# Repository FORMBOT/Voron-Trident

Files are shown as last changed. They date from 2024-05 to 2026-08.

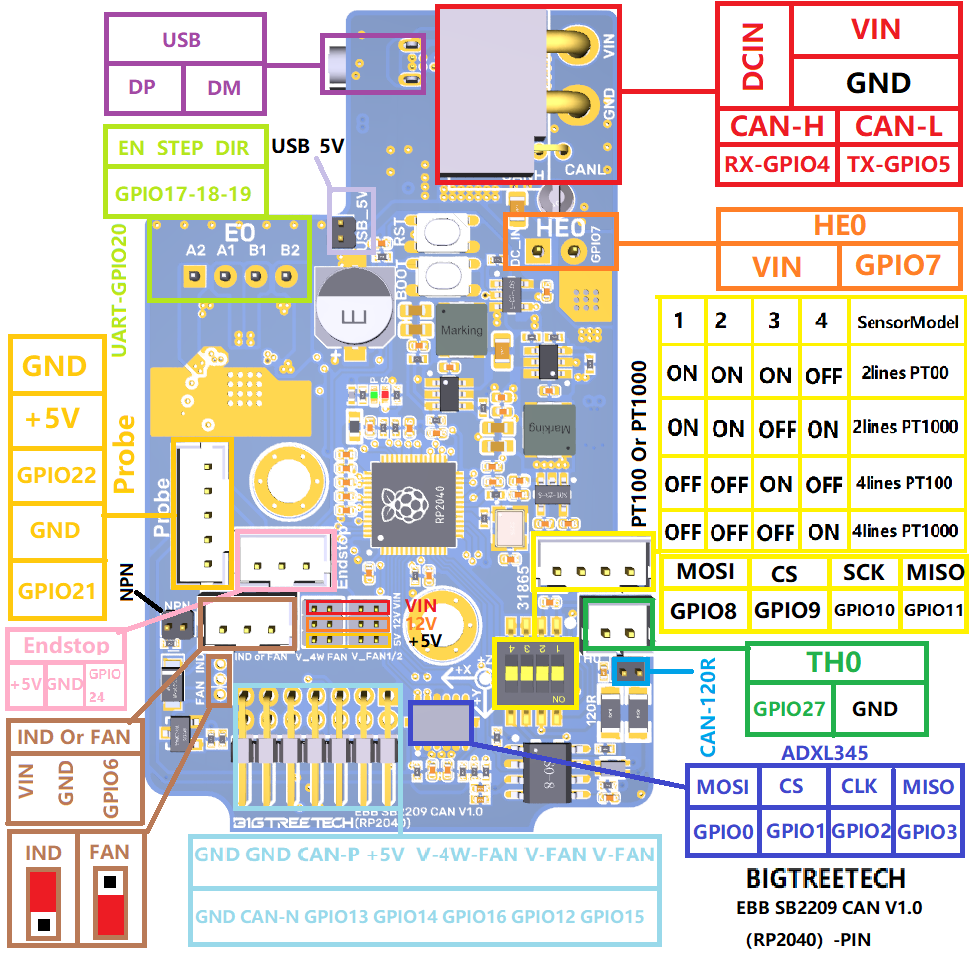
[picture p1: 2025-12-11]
Diagrams/Pins/SB2209 RP2040 Pinout.png

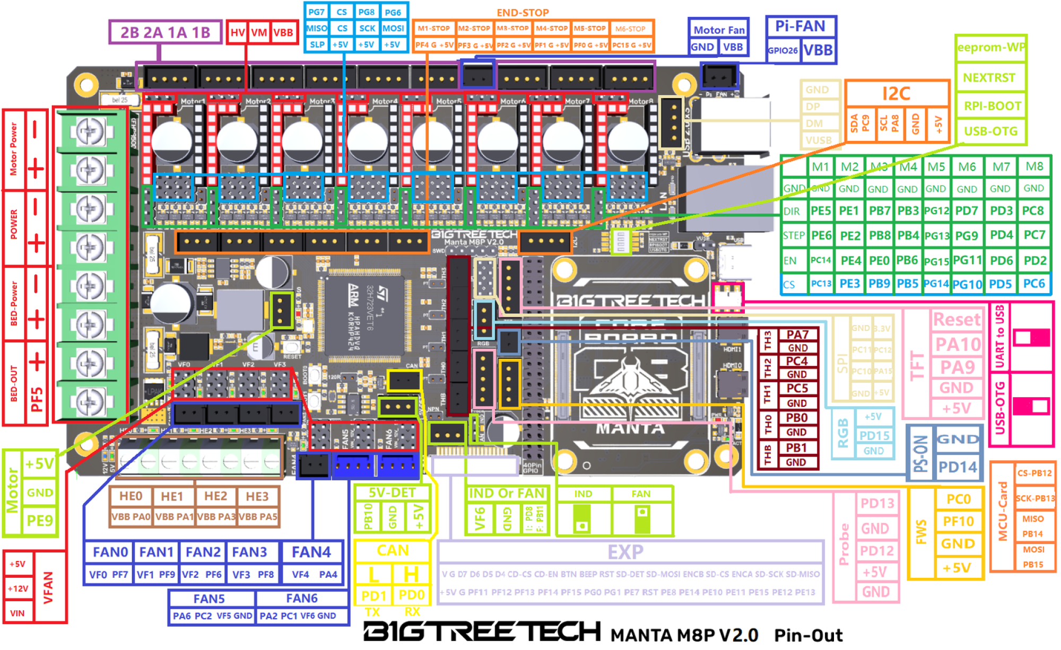
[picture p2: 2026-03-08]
Diagrams/Pins/BIGTREETECH MANTA M8P V2-0 PinOut.png

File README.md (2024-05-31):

# Custom STL´s for the Formbot Voron-Trident R1 Pro Kit
https://www.formbot3d.com/products/voron-trident-r1-pro-corexy-3d-printer-kit-with-best-quality-parts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

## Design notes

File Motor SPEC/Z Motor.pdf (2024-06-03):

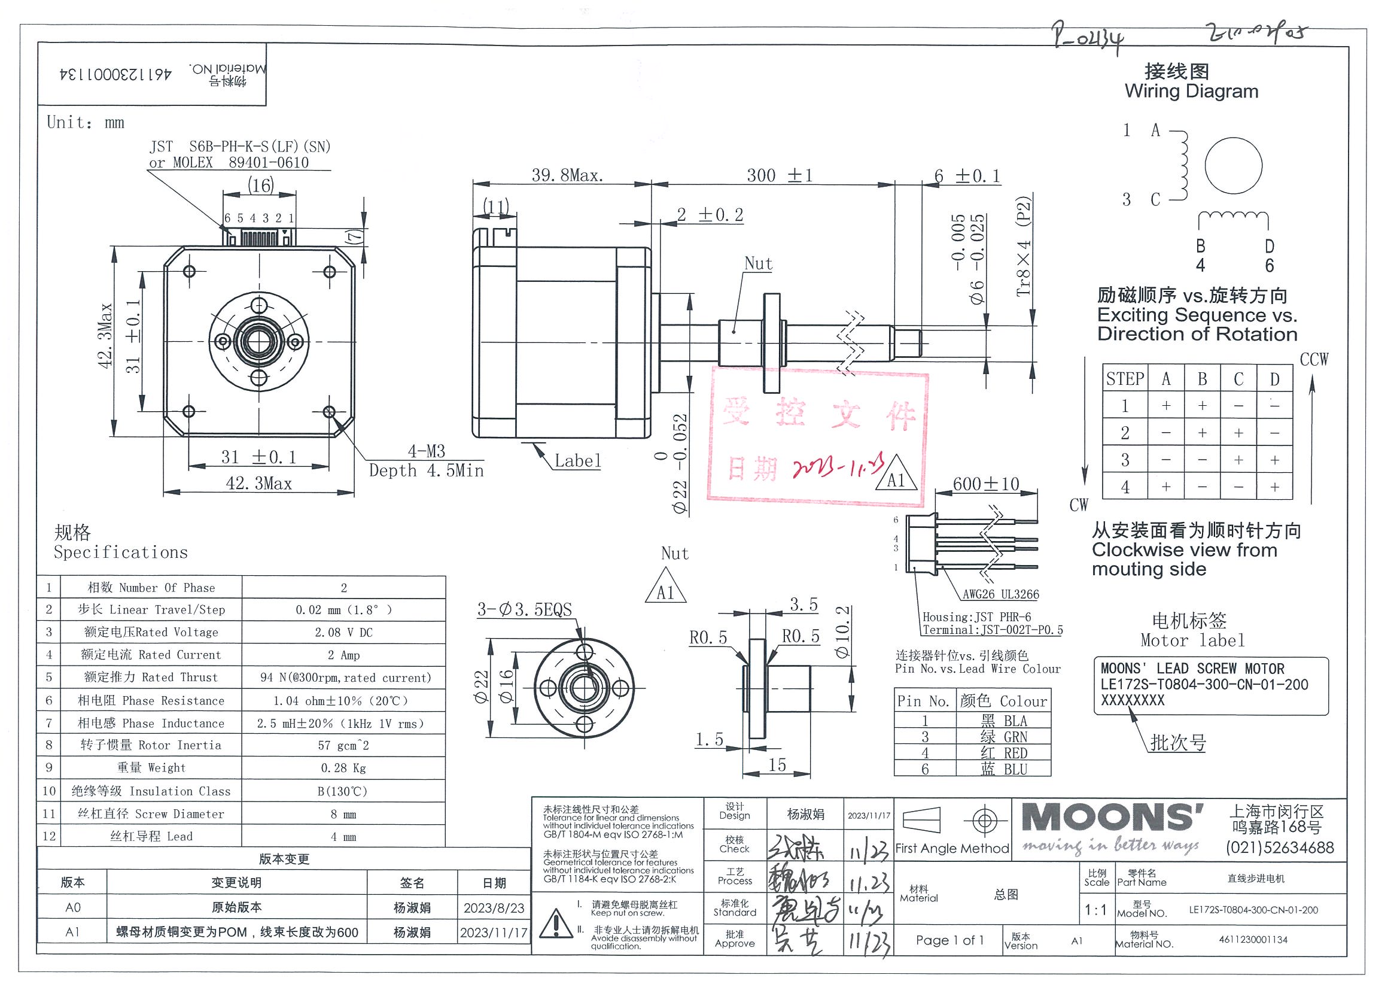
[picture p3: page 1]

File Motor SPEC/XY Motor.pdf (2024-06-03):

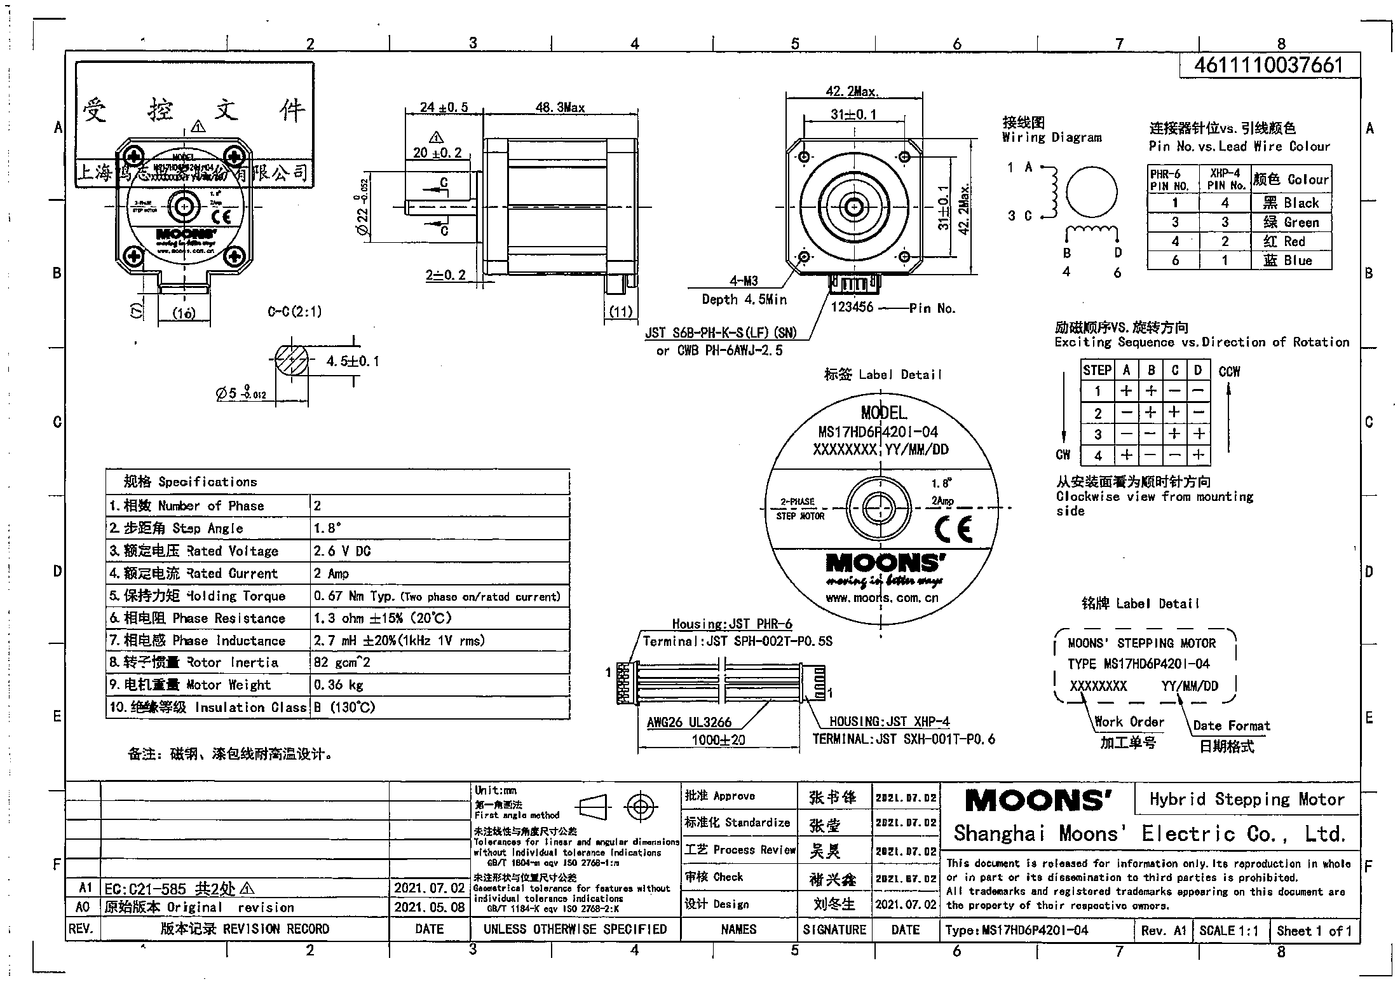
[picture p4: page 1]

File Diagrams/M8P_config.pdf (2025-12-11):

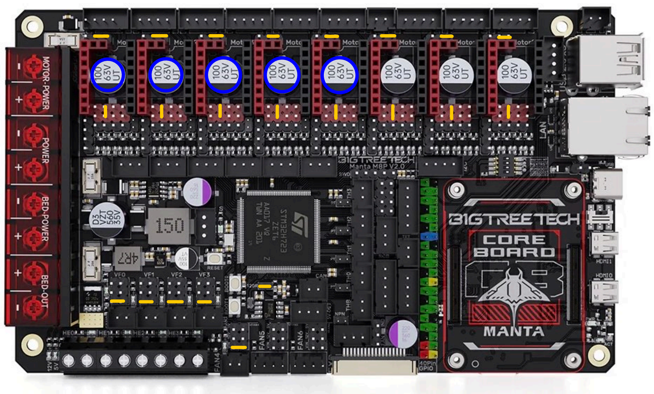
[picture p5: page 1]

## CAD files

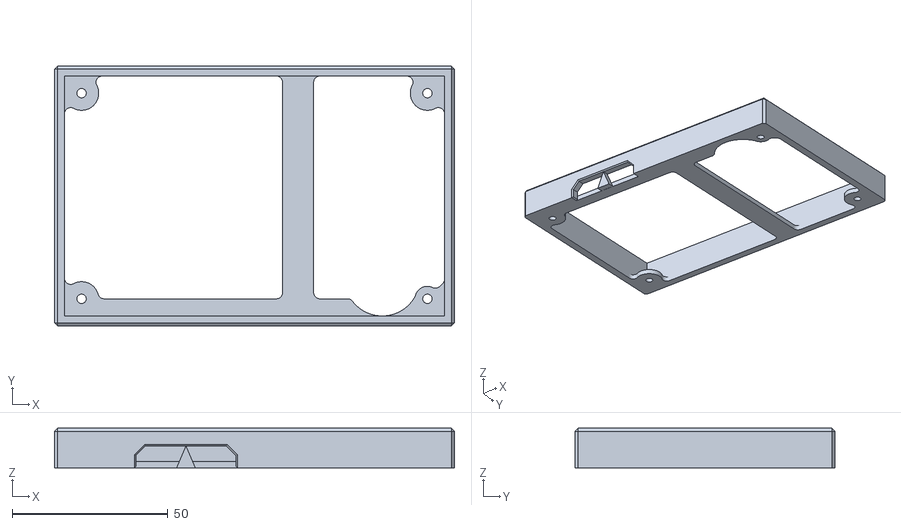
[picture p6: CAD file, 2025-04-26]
STL/Accent/BTT HDMI5 V1_2 mount frame_Regular.stl
128.4 x 83.4 x 12.7

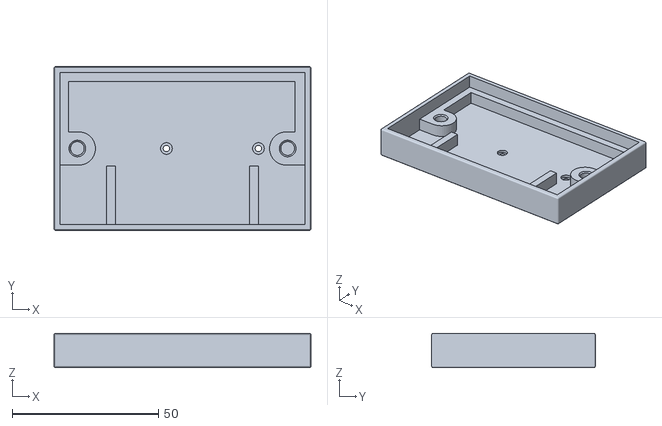
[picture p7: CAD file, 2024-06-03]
STL/Primary/3-6.STL
88.0 x 56.0 x 11.8

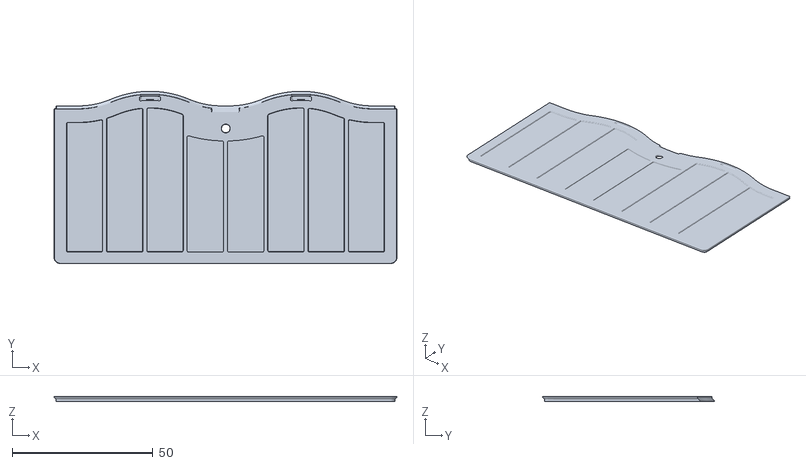
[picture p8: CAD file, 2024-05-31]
STL/Primary/Nevermore/Trident_Bed_Mount_XL_Cartridge_LID.stl
122.0 x 61.3 x 1.78

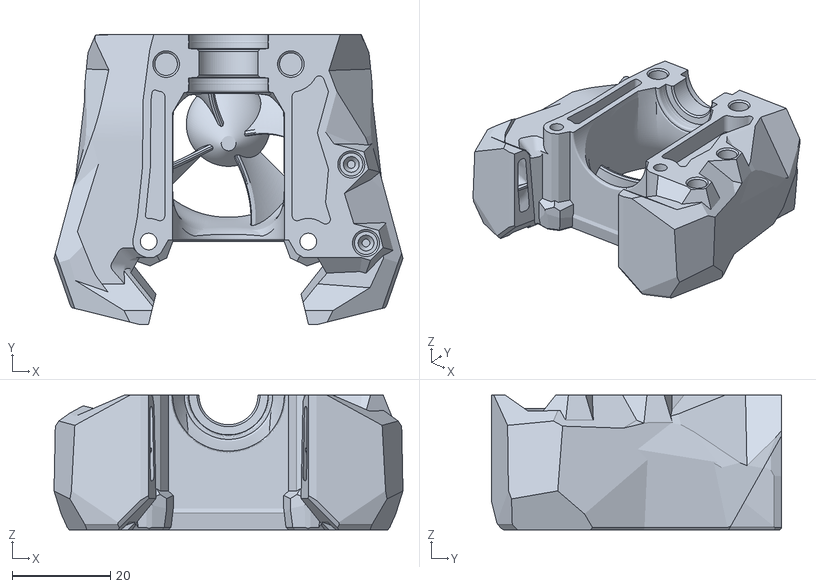
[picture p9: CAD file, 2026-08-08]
STL/Stealthburner/Stealthburner/stealthburner_printhead_v6_r6_front.stl
71.1 x 59.1 x 27.4

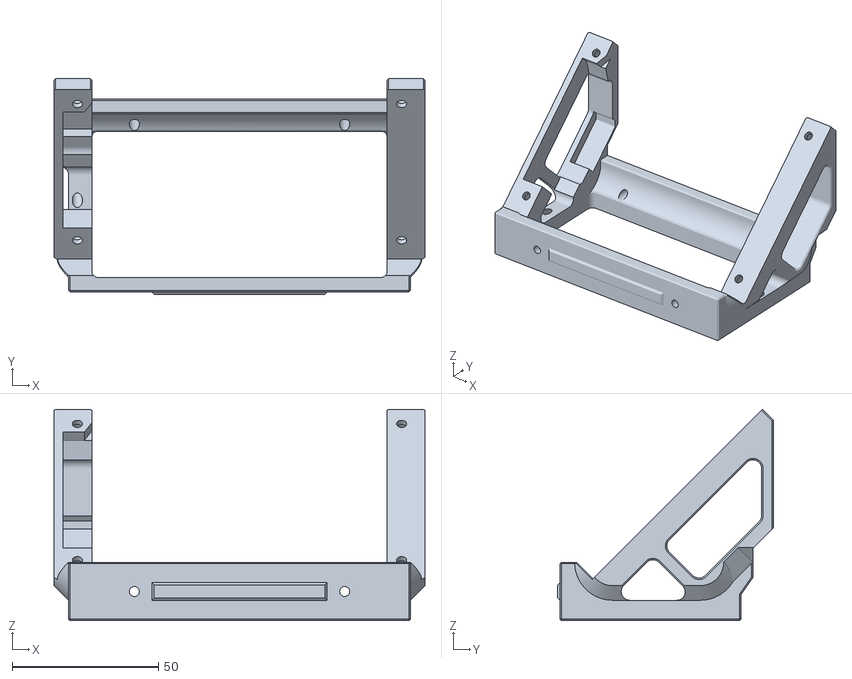
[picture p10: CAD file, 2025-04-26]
STL/Accent/BTT HDMI5 V1_2 mount bracket_Regular.stl
127.0 x 73.8 x 72.4

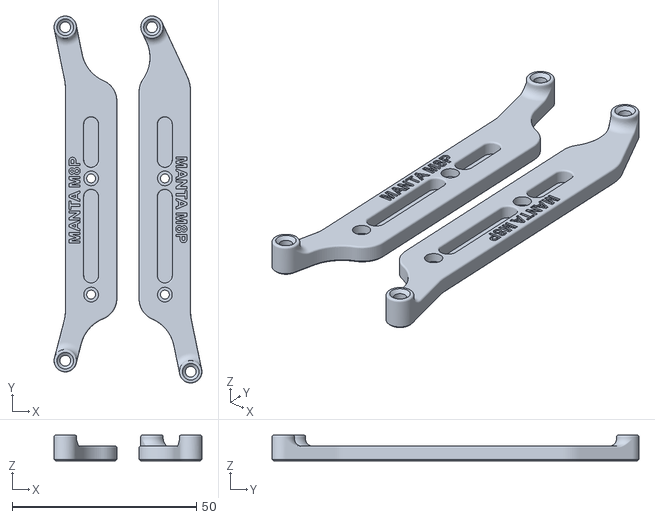
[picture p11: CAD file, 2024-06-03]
STL/Primary/Manta_M8P_2pc.stl
40.1 x 99.5 x 7.00

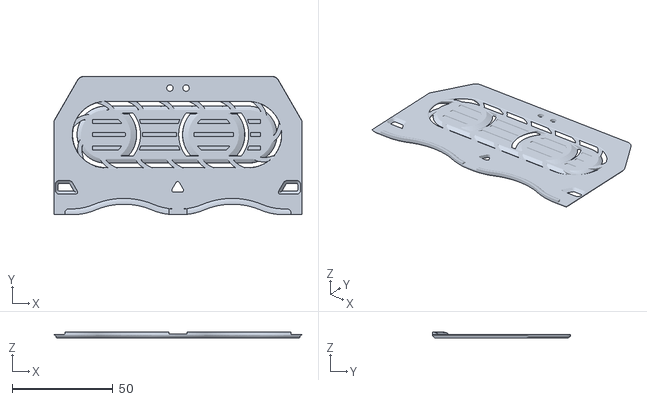
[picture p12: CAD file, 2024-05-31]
STL/Primary/Nevermore/Trident_Bed_Mount_Plenum_Lid_r1.stl
122.8 x 68.5 x 2.80

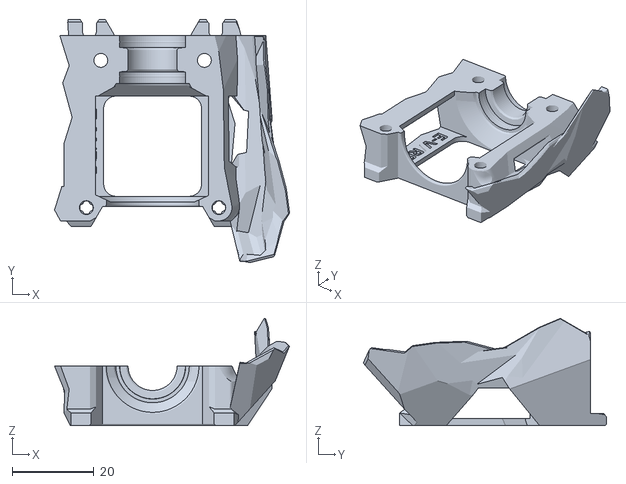
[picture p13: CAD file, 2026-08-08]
STL/Stealthburner/Stealthburner/stealthburner_printhead_v6_r6_rear_cw2.stl
57.7 x 59.7 x 26.3

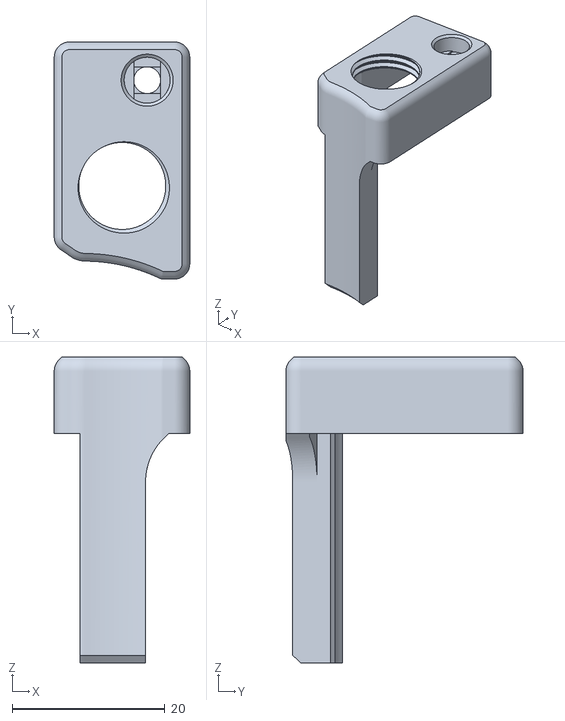
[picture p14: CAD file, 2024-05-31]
STL/Accent/PG7 Gantry Adapter.stl
17.7 x 31.0 x 40.0

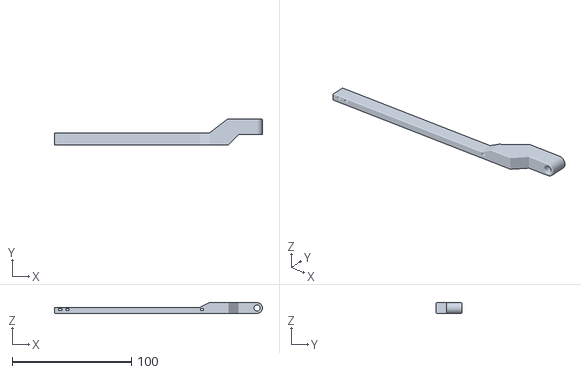
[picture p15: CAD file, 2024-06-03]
STL/Primary/cable support rod for CAN.STL
174.5 x 21.5 x 9.00

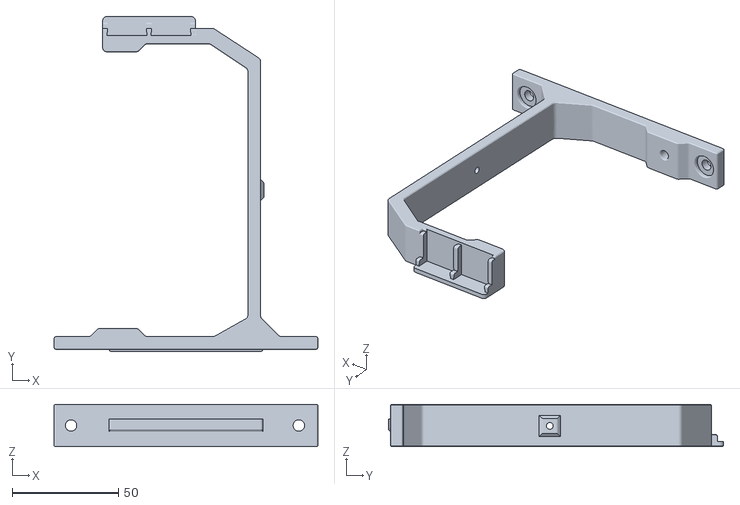
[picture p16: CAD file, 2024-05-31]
STL/Primary/Nevermore/trident_bed_mount_bracket_right_r1.stl
124.4 x 157.9 x 20.0

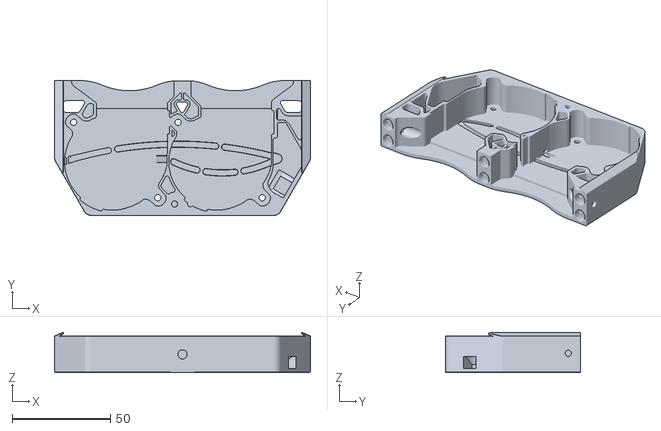
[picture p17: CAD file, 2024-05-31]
STL/Primary/Nevermore/Trident_Bed_Mount_Plenum.stl
130.0 x 68.6 x 20.5

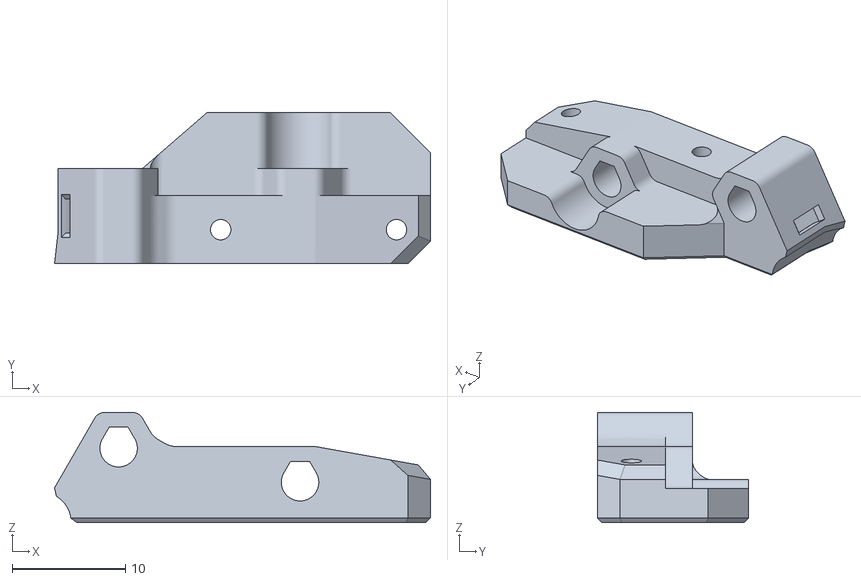
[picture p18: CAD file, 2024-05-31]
STL/Primary/sb_adxl_mount_generic_15.5mm_c_c.stl
33.2 x 13.4 x 9.70

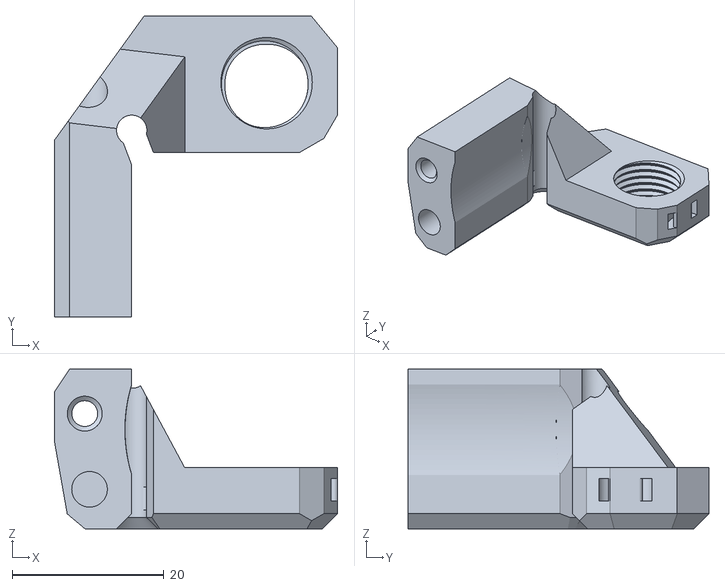
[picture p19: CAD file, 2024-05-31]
STL/Primary/Anchor v2.stl
37.3 x 39.7 x 21.1

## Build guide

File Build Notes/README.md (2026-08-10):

## Functional parts build notes (to get the Printer up and running)

Start with the [Stock Voron Trident R1 Manual](https://drive.google.com/file/d/1SZPV2CbrWAcEAtXU0fp9lZ_o1P9Tl-v9/view?usp=sharing) (the one on the Voron Trident R1 Git is not the most recent one).

Be aware that the vT Manual uses a 250mm Version of the Trident, so some dimensions may seem wrong if you build a 300mm/350mm Version.

### P. 48 Trident manual:

Skip this step, we use physical endstops and no hall effect ones.

### P. 56-60 Trident manual:

If you are building a 300mm machine you will need to start you screws from the second screw hole in the rails leaving the end holes open to allow space for T-nuts at later steps. Small reminder: The carriages are designed to slide along the rail easily. This unfortunately also includes sliding off the rails. Dropping the carriage likely irreparably damages it. ALWAYS put the little black rubber Carriage stoppers back on the rail (into the holes without screws) until your printer ist up and runnning!

### P. 100-101 Trident manual:

Skip these steps, you wont use either the inductive probe or a Cable chain on XY.

### P. 111 Trident manual:

Again, if you are building a bigger printer than the 250mm version, start at the outer holes and screw the rail down every second hole. Small reminder (again): The carriages are designed to slide along the rail easily. This unfortunately also includes sliding off the rails. Dropping the carriage likely irreparably damages it. ALWAYS put the little black rubber Carriage stoppers back on the rail (into the holes without screws) until your printer ist up and runnning!

### P.114 Trident manual:

Install all 4 screws on the right XY Joint.

### P. 115 Trident manual:

Leave this step out, you dont use a cable chain on X and Y.

### P. 122-123 Trident manual:

You use a different X carriage / Probe. Fix the belts with some tape and proceed with the belt Routing. After you routed the belts, fix them on the other side with some tape as well.

### P. 131-133 Trident manual:

Skip these steps, you will do it later after tap is assembled.

### P. 133 Trident manual:

X Carriage: After finishing the AB-Belts Routing, switch to the [TAP Manual](https://github.com/VoronDesign/Voron-Tap/tree/main/Manual). Optotap is used as the sensor.

Be sure to take a look into the R8\_errata.md document, it Highlights some important changes from the Manual and install the X Endstop switch.

### P. 33 Tap Manual:

After you have installed Tap successfully and have the AB belts fixed in the tap carriage, switch to page 134 of the Trident Manual.

### P. 135-137 Trident manual:

Skip these steps since you don't use the stock X carriage but instead you use tap.

### P. 144-145 \& 159 Trident manual:

You don't use this endstop. Your endstop is Tap.

### P. 162/163 Trident manual:

Switch to the [Stealthburner manual](https://github.com/VoronDesign/Voron-Stealthburner/tree/main/Manual).

### P. 13 Stealthburner manual:

You use a Toolhead PCB, so install these two heat inserts.

### P. 14 Stealthburner manual:

Skip

### P. 30 Stealthburner manual:

Follow [this Video Guide](https://www.youtube.com/watch?v=ly22qmB3NxE&t=1s) on how to set the gear mesh on your CW2.

Follow [this video Guide](https://www.youtube.com/watch?v=L1gxBCiE0pk) on how to set the Anti-Squish as well.

### P. 31 Stealthburner manual:

Skip for now, we will install our Version of the Anchor later.

### P. 34 Stealthburner manual:

You dont need to fix the Cable Cover down with the m3x6 BHCS now, you will need to access this later.

### P. 36-43 Stealthburner manual:

All Hotends are mounted in a similar pattern and pretty self-explaining, your hotend mount and hotend will look different.

### P. 46-51 Stealthburner manual:

Be very careful with the cables, you can easily rip them off the LED PCB which leads to this LED and the following ones not working.

### P. 53 Stealthburner manual:

Be sure that your fan blows in the right Direction. Look at the arrows on the fan. Additionally, the Sticker on the fan is on the back pointing towards the Hotend. You want the fan to blow air into the hotend, not trying to pull the air out. This destroys your fan and your whole hotend mount because of heatcreep.

### P. 56 Stealthburner manual:

You dont need to screw the 5015 fan into the SB Face, you will install the SB0000 Fan PCB there later.

### P. 58 Stealthburner manual:

All parts of the Stealthburner are now pretty much finished. Now you will need to install the Can-Board on there and do some basic wiring. Switch to the [SB2209 RP2040 Manual](https://github.com/bigtreetech/EBB/tree/master/EBB%20SB2209%20CAN%20%28RP2040%29/Build%20Guide).

### P. 02 SB2209 manual:

Now you need to screw down the 5015 fan with the SB0000 PCB :)

### P. 03/04 SB2209 manual:

You need to select Vin (24V) for all fans. Be sure to wire Gnd to Gnd and 24V to 24V! Otherwise you will experience magic smoke later.

### P. 05 SB2209 manual:

Skip

### P. 06 SB2209 manual:

Be sure to wire Gnd to Gnd, Signal to Signal and 24V to 24V! Otherwise you will experience magic smoke later.

### P. 13 SB2209 manual:

You Need to set the switch to 1: on; 2: on; 3: off; 4: on

### P. 15 SB2209 manual:

Skip

### P. 16 SB2209 manual:

Be sure to use the endstop labeled "To CAN\_Endstop" which is the one with the short wires.

### P. 18 SB2209 manual:

Skip

### P. 19 SB2209 manual:

Skip, Stealthburner will be assembled later.

### P. 24 SB2209 manual:

You will need to Strip down the Isolation a bit so you have enough cable length to connect the cable to the PSU and to the Can port. Go back to the Tap Manual page 34 now, flashing the toolhead will be done later.

Use the tight cable sleeve around the cable.

### P. 36 Tap manual:

Stealthburner and Tap are now completed and installed. Switch back to p. 164 of the original Trident manual.

### P. 173 Trident manual:

Rotate the din rails 90° compared to the original layout.

### P. 181-183 Trident manual:

Skip; Raspberry Pi mounting and 5v PSU mounting is not needed. Instead, mount the CB1 / CM4 on the Manta.

### P. 191 Trident manual:

You use the 3in6 Power Distributor instead.

### P. 195 Trident manual:

another small reminder, you don't use a 5v PSU.

### P. 196 Trident manual:

small reminder, you dont use a Raspberry Pi.

### P.198-200 Trident manual:

Skip; TAP is your Z-Endstop, your X Endstop sits on Tap and your Y endstop will be mounted on the A Motor mount later.

### P. 202-205 Trident manual:

Skip these steps, instead configure your Manta like this:

[M8P\_v2 Jumper / Driver marking](https://github.com/FORMBOT/Voron-Trident/blob/main/Diagrams/M8P_config.pdf)

Place a Jumper on all yellow marked pins and place the TMC2209s with attached heatsink on all driver ports with a blue circle after installing the jumpers.

### P. 210/211/216 Trident manual:

Leave the cables to the 5v PSU out.

### P. 217 Trident manual:

Skip, you dont use a standart Raspberry.

### P. 218 Trident manual:

The Z-Endstop cables are not needed.

### P. 218-219/221-231/233-237 Trident manual:

For a better Overview of the wiring, use the [wiring diagram](https://github.com/FORMBOT/Voron-Trident/blob/main/Diagrams/Wiring%20Diagram%20of%20Trident%20R1%20Pro.pdf).

Connect the B motor (left motor) to X Motor, connect the A motor (right motor) to Y Motor.

Connect the CAN-Cable to the right CAN-Port on the M8P and 24V / GND to the 24V PSU. If you think the cables are not Long enough, you haven't done [this step](https://github.com/FORMBOT/Voron-Trident/tree/main/Build%20Notes#p-24-sb2209-manual).

### P. 232 Trident manual:

Route the Y Endstop cable and the A Motor cables down like the B Motor cable (but on the right side of the printer).

### P. 242-244/257 Trident manual:

Skip these steps and instead mount the klipperscreen.

### P. 258 Trident manual:

Don't close the electronics compartment yet, you will need to acces this while flashing the boards.

### P. 281 Trident manual:

Use the big cable sleeve around the exhaust fan cable (if you use the stock exhaust).

#### Don't power on the printer if you are not 100% sure you wired everything correct! And have a look into [this](https://github.com/FORMBOT/Voron-Trident/blob/main/Diagrams/Instruction%20of%20Trident%20R1%20Pro.pdf).

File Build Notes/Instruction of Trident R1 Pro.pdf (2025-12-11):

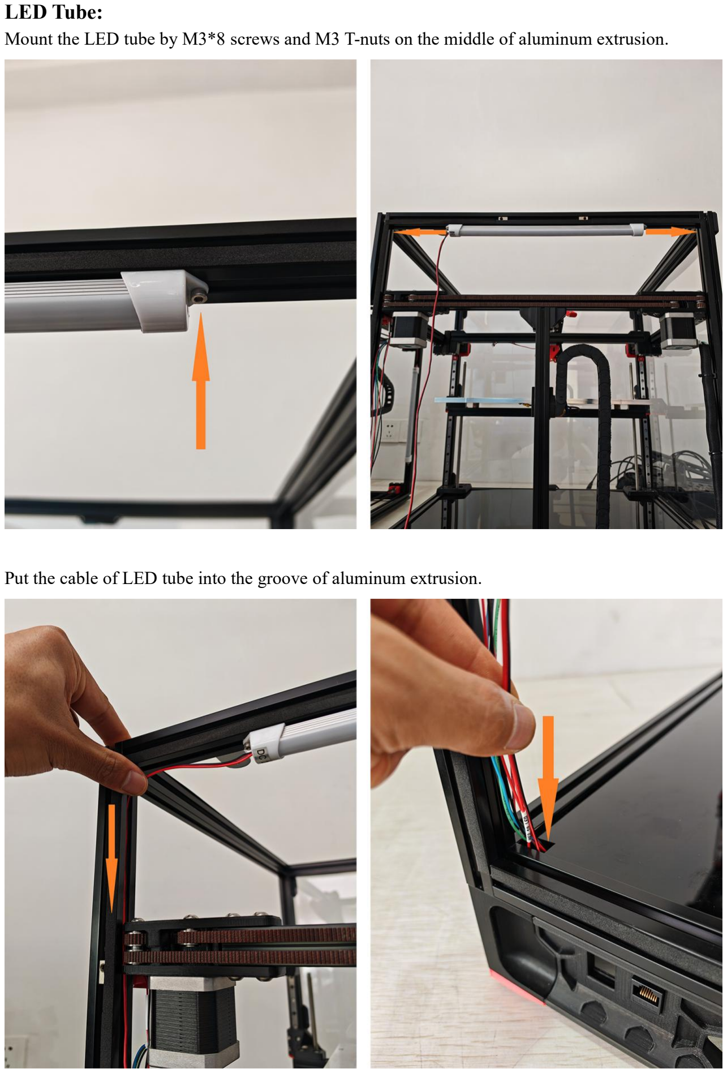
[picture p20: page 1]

LED Tube:
Mount the LED tube by M3*8 screws and M3 T-nuts on the middle of aluminum extrusion.

Put the cable of LED tube into the groove of aluminum extrusion.

Plug the cable onto mainboard as showed below, the red wire to “+”, the black wire to “-”.

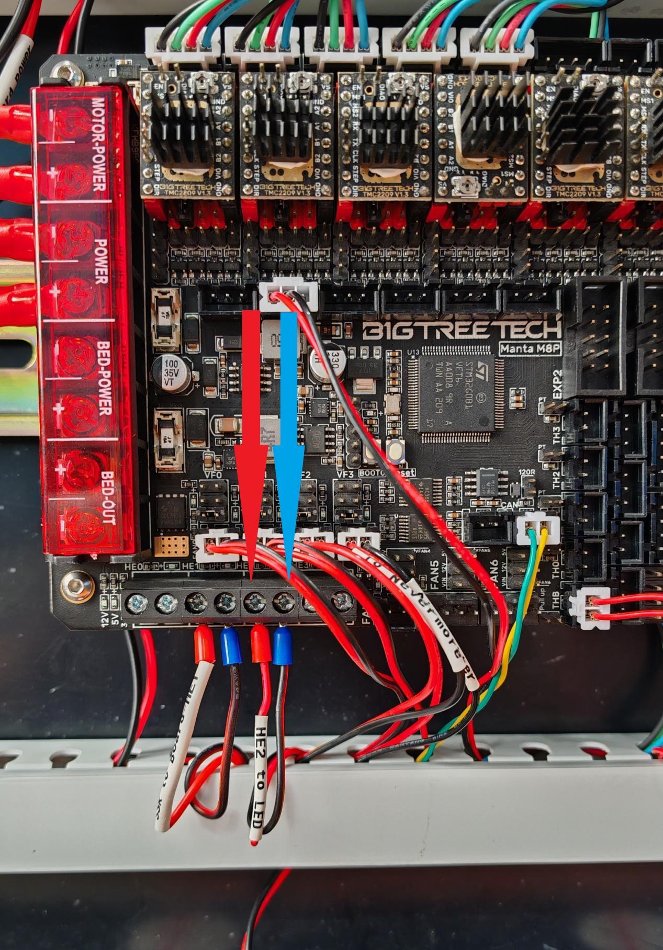
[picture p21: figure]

Filament Runout Sensor:
Take out the sensor and cable as showed below.

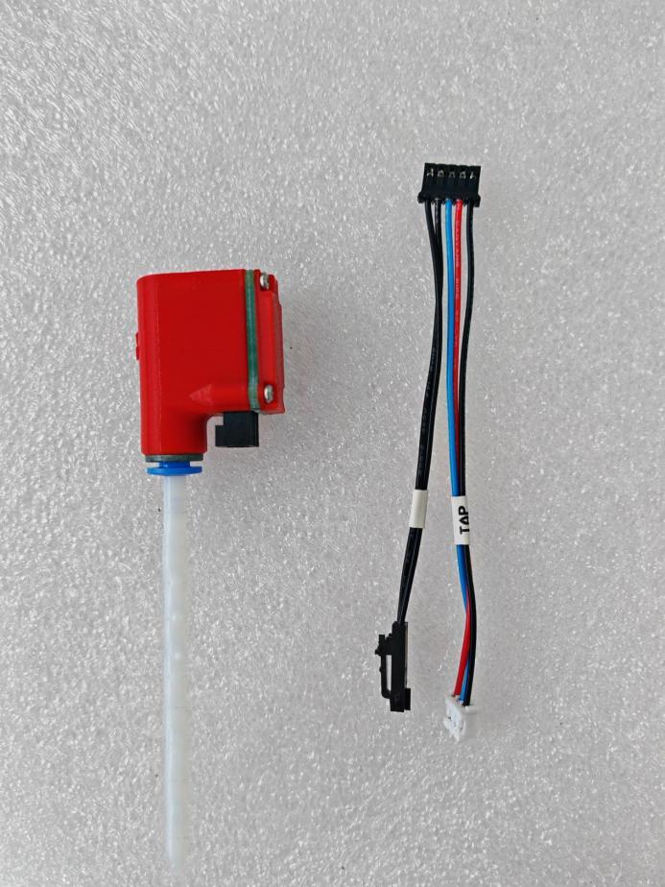
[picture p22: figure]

Plug the cable into below connector on extruder.

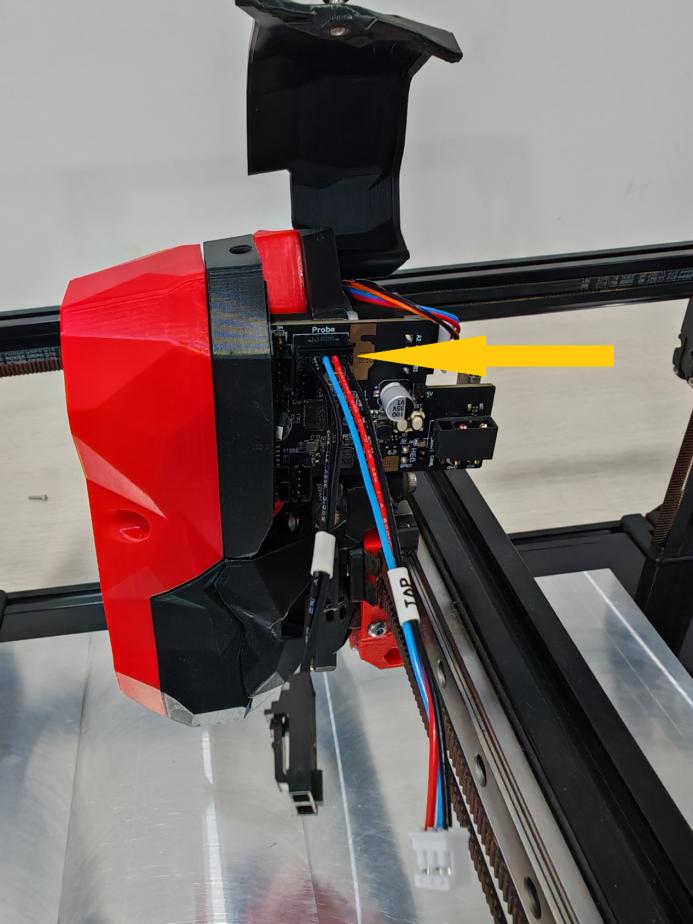
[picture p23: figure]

Plug the wires of TAP to below connector.

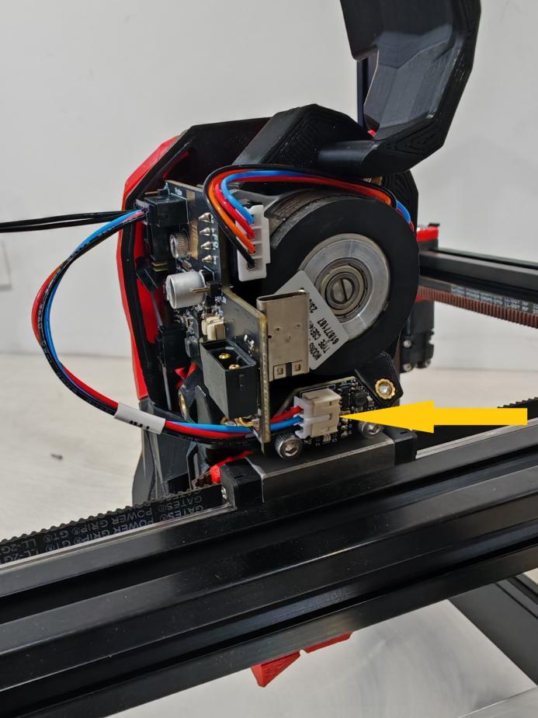
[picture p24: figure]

Pass the wires of filament runout sensor through below hole, then plug it onto sensor directly.

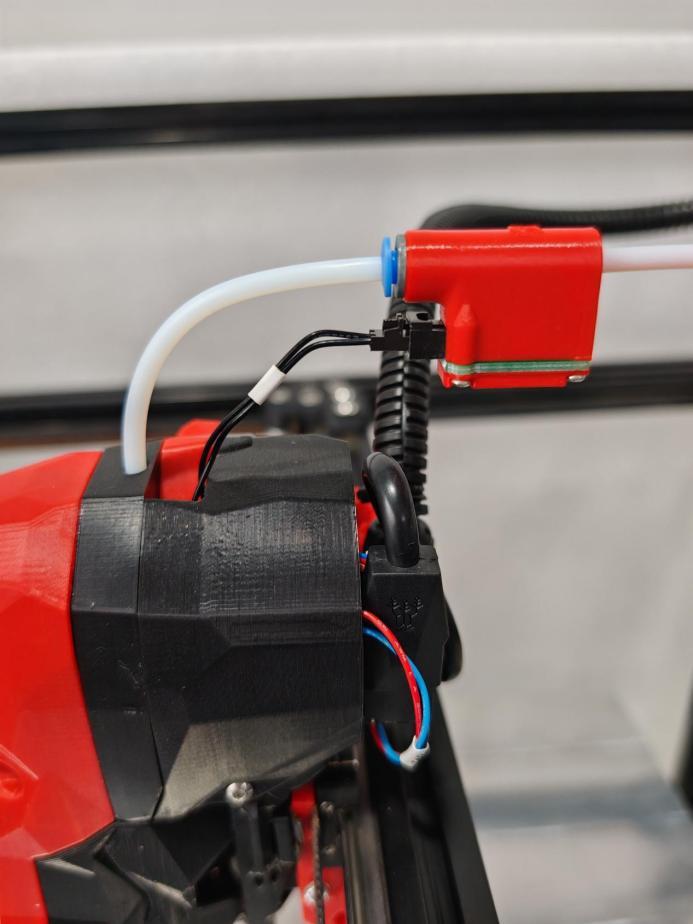
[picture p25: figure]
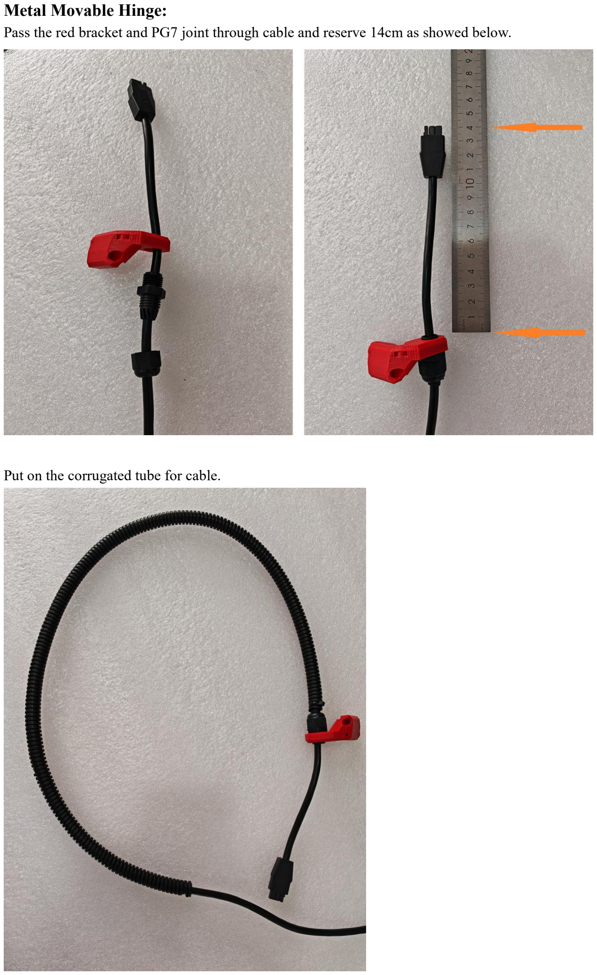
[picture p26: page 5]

Metal Movable Hinge:
Pass the red bracket and PG7 joint through cable and reserve 14cm as showed below.

Put on the corrugated tube for cable.

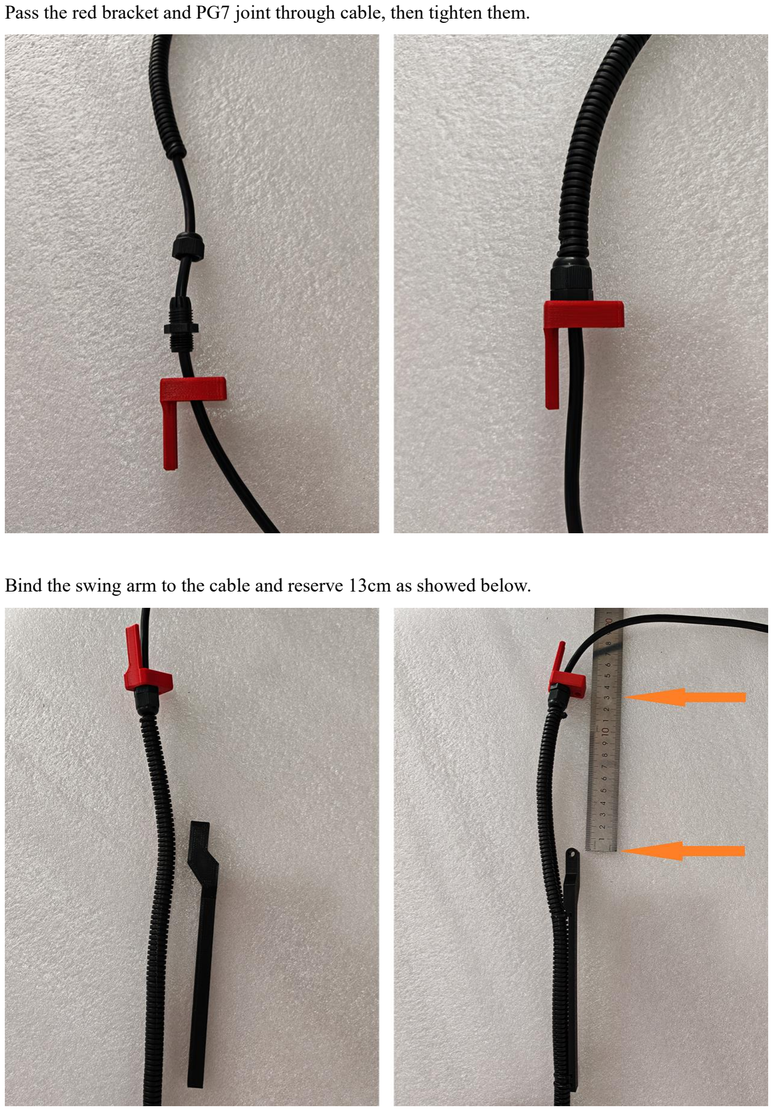
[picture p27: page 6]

Pass the red bracket and PG7 joint through cable, then tighten them.

Bind the swing arm to the cable and reserve 13cm as showed below.

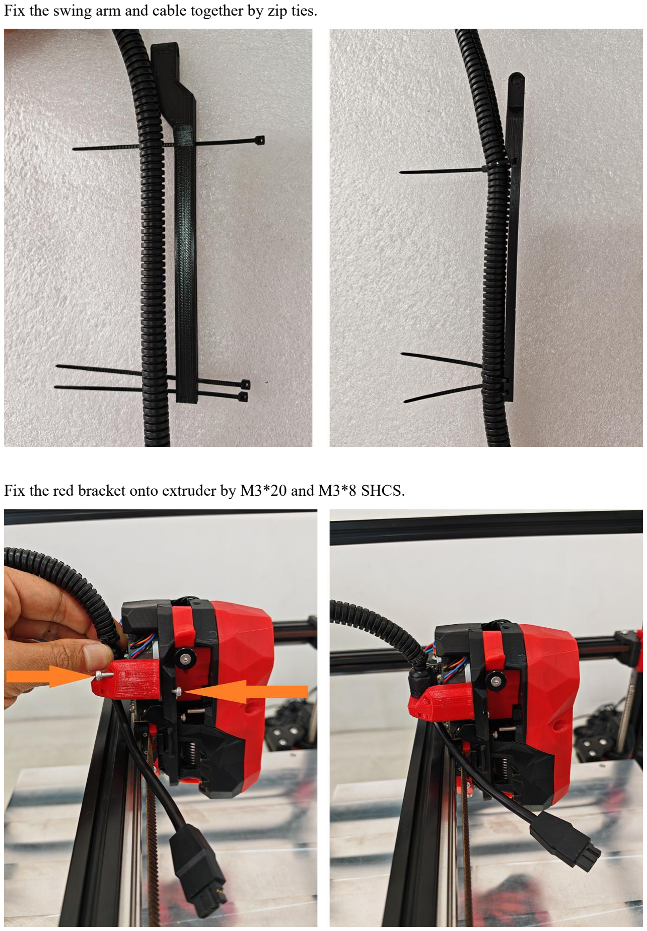
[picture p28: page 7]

Fix the swing arm and cable together by zip ties.

Fix the red bracket onto extruder by M3*20 and M3*8 SHCS.

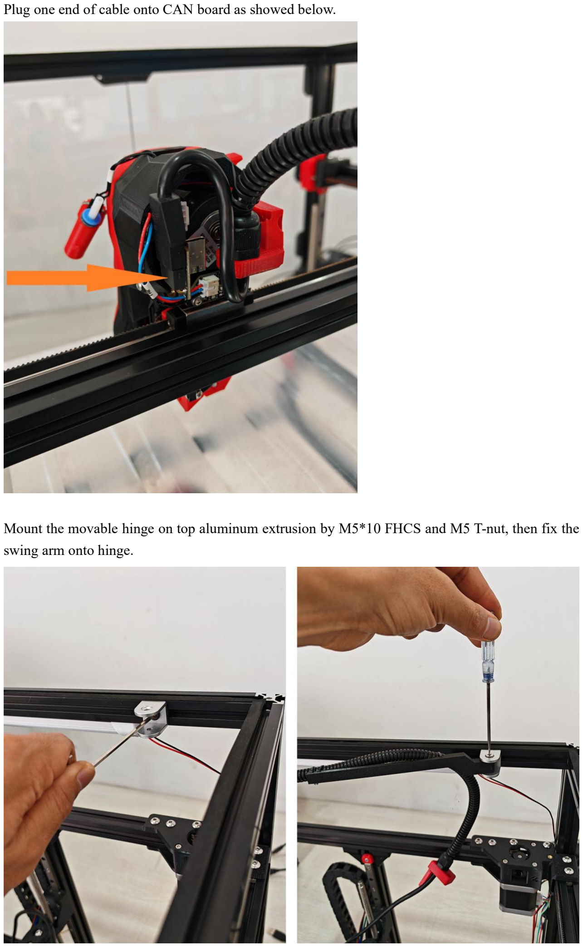
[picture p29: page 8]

Plug one end of cable onto CAN board as showed below.

Mount the movable hinge on top aluminum extrusion by M5*10 FHCS and M5 T-nut, then fix the swing arm onto hinge.

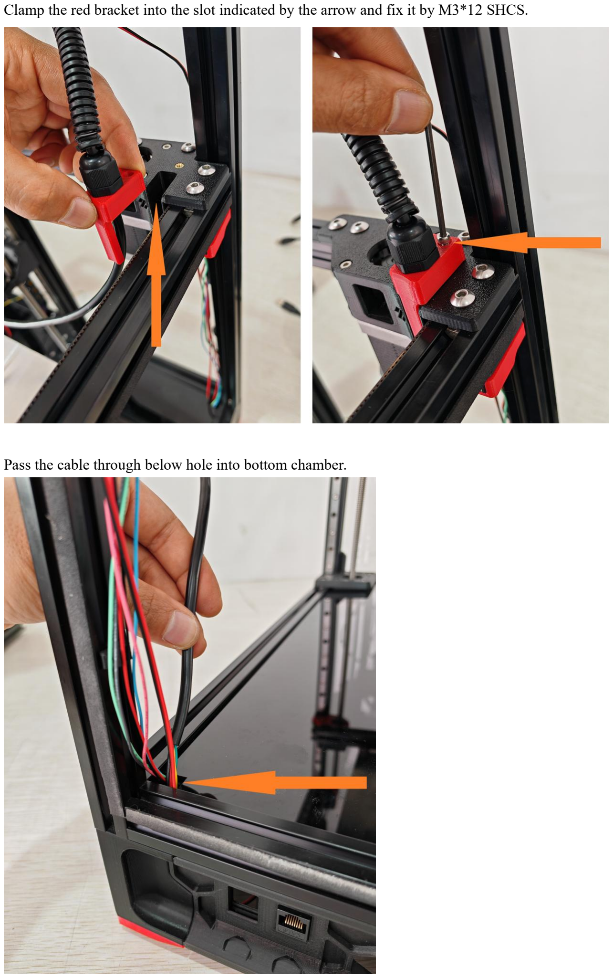
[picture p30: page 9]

Clamp the red bracket into the slot indicated by the arrow and fix it by M3*12 SHCS.

Pass the cable through below hole into bottom chamber.

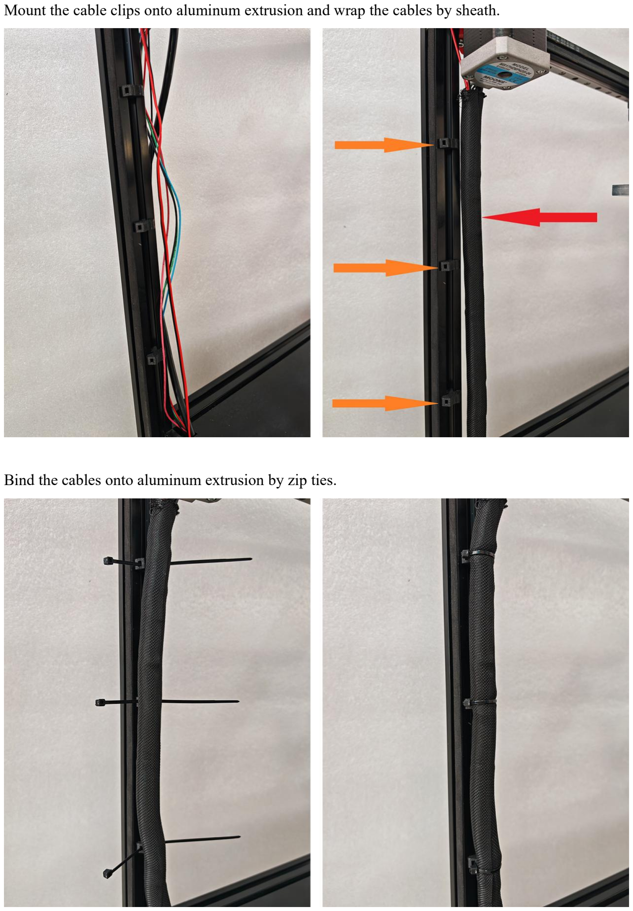
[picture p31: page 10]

Mount the cable clips onto aluminum extrusion and wrap the cables by sheath.

Bind the cables onto aluminum extrusion by zip ties.

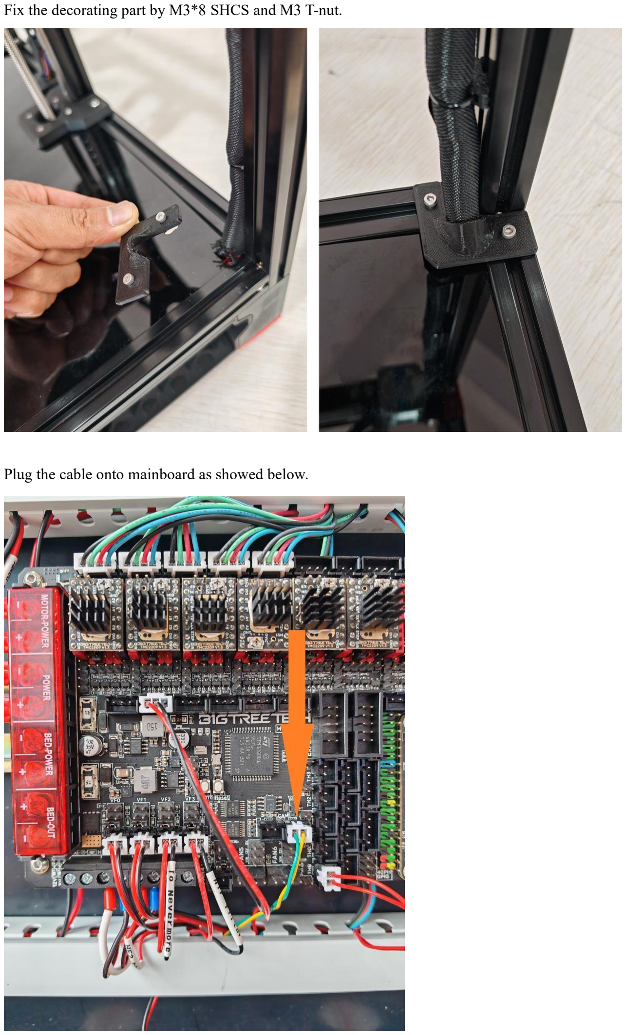
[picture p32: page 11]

Fix the decorating part by M3*8 SHCS and M3 T-nut.

Plug the cable onto mainboard as showed below.

Connect below two wires to power supply, the red wire to “+”, the black wire to “-”.

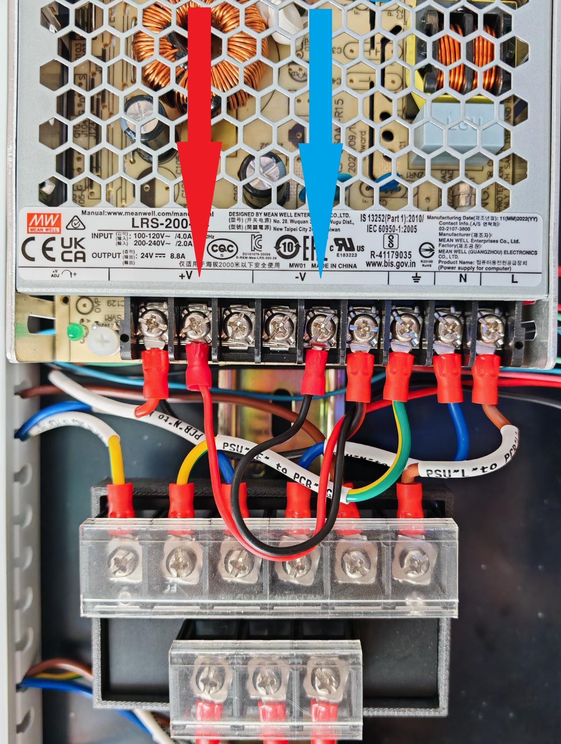
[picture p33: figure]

Nevermore Air Filter:
Iron M3 brass nuts into below holes.

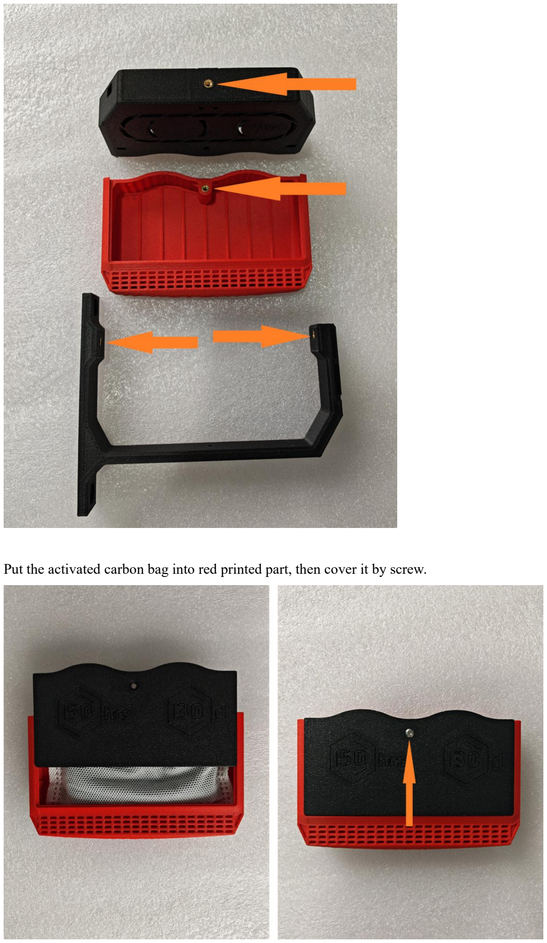
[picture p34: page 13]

Put the activated carbon bag into red printed part, then cover it by screw.

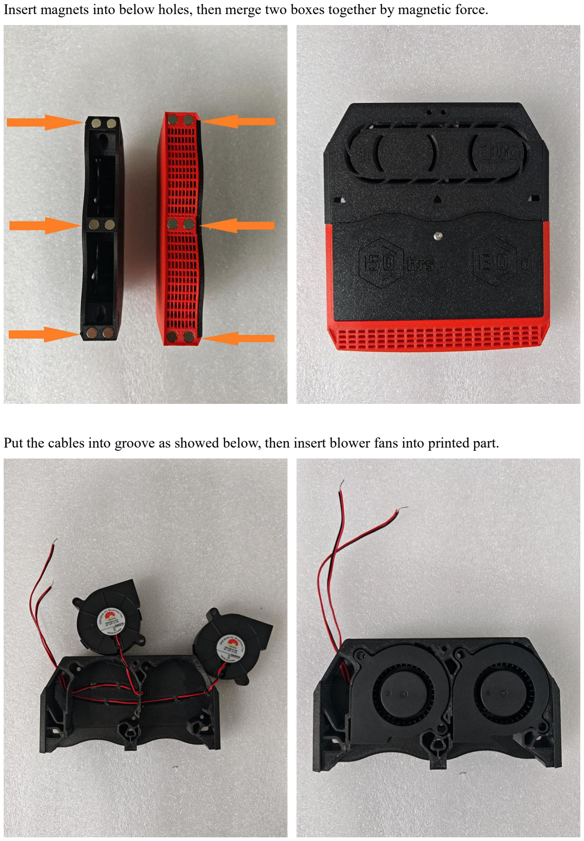
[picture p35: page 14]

Insert magnets into below holes, then merge two boxes together by magnetic force.

Put the cables into groove as showed below, then insert blower fans into printed part.

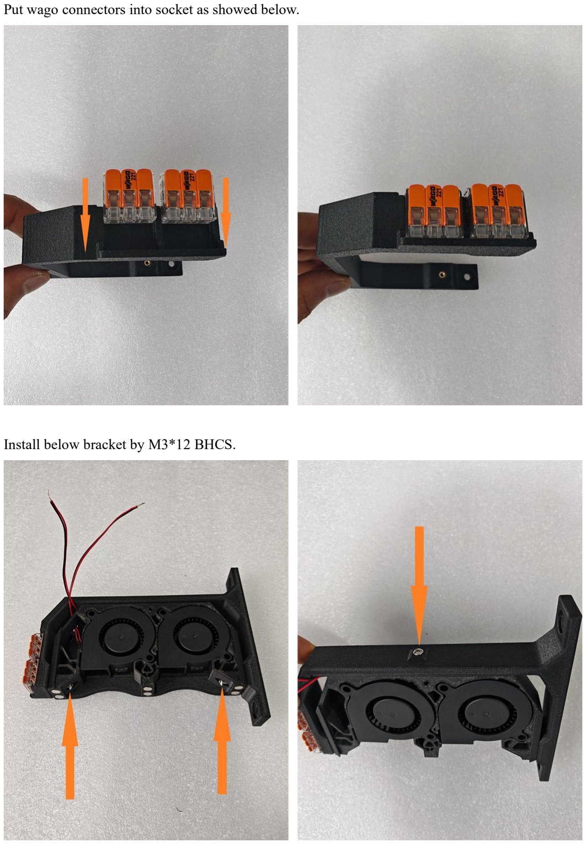
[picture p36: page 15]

Put wago connectors into socket as showed below.

Install below bracket by M3*12 BHCS.

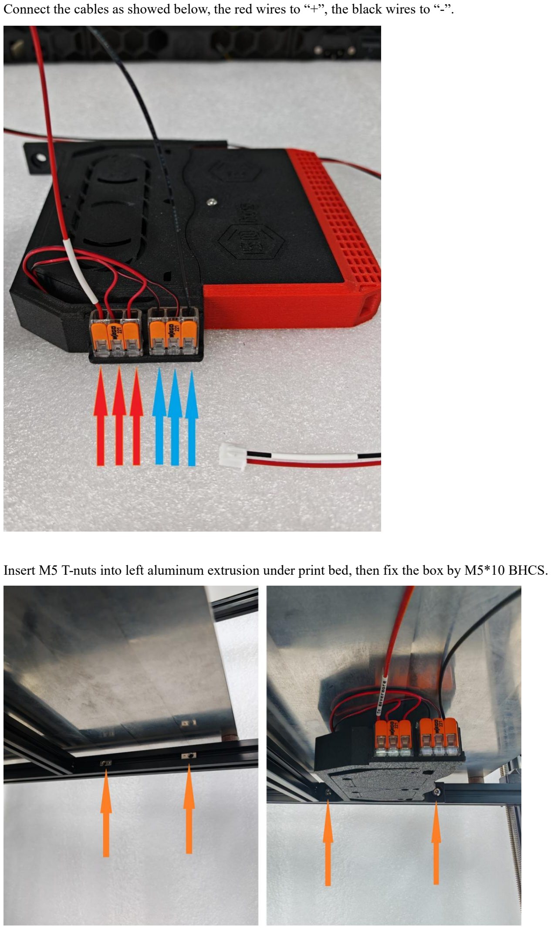
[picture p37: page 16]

Connect the cables as showed below, the red wires to “+”, the black wires to “-”.

Insert M5 T-nuts into left aluminum extrusion under print bed, then fix the box by M5*10 BHCS.

Merge two boxes together by magnetic force.

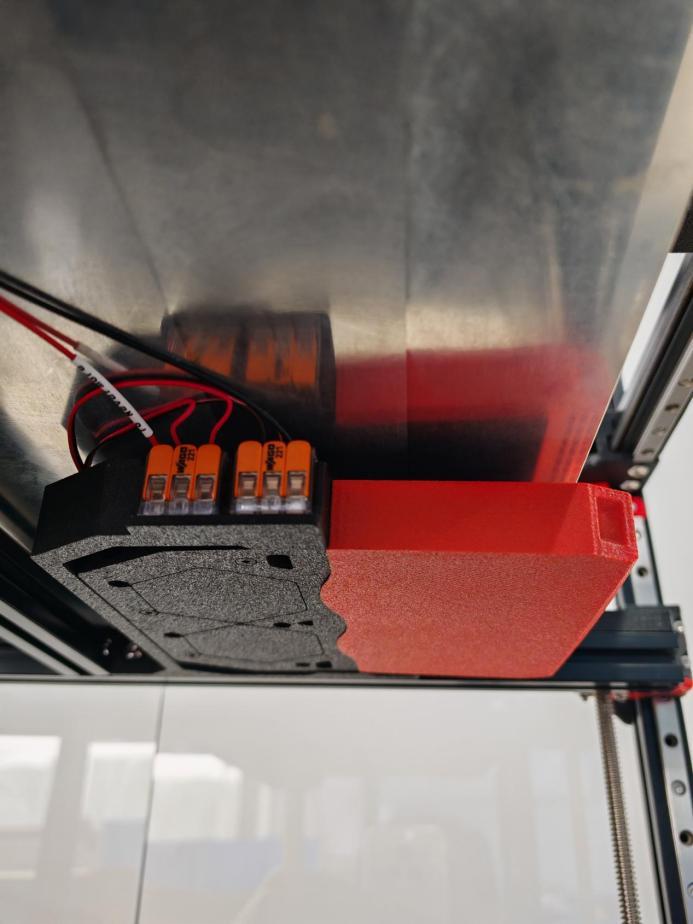
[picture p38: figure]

Pass the cables through chain into bottom chamber.

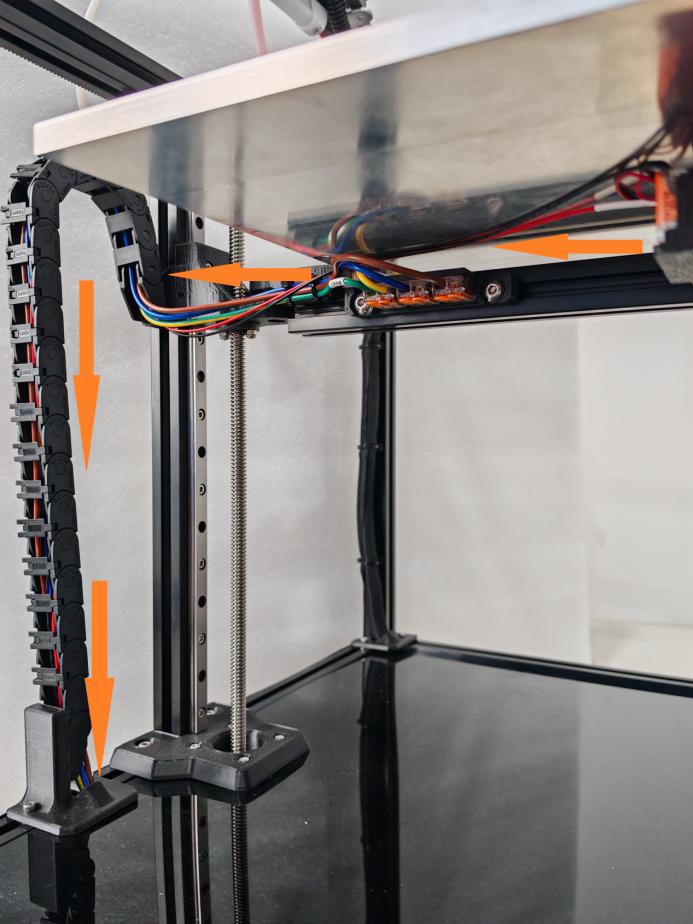
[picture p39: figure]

Finally, plug it onto mother board as showed below.

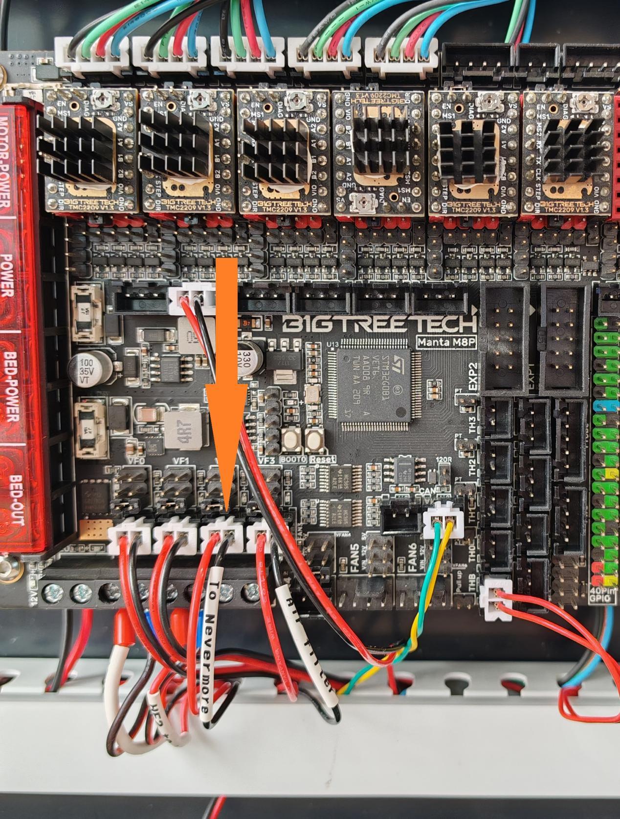
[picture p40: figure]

Referential Links:

Voron Official Build Guide: https://github.com/VoronDesign/Voron-Trident/tree/main/Manual

Stealthburner Extruder:
https://github.com/VoronDesign/Voron-Stealthburner/blob/main/Manual/Assembly_Manual_SB.p df (https://github.com/VoronDesign/Voron-Stealthburner/blob/main/Manual/Assembly_Manual_SB.pdf)

TAP R8 Leveling Sensor:
https://github.com/VoronDesign/Voron-Tap/blob/main/Manual/Assembly_Manual_Tap.pdf

HDMI 5" V1.2 Screen:
https://www.printables.com/model/926845-btt-hdmi5-v12-display-mount-voron

Manta M8P V2.0+CB1 Board:
https://github.com/bigtreetech/Manta-M8P/blob/master/V2.0/BIGTREETECH%20MANTA%20 M8P%20V2.0%20User%20Manual.pdf (https://github.com/bigtreetech/Manta-M8P/blob/master/V2.0/BIGTREETECH%20MANTA%20M8P%20V2.0%20User%20Manual.pdf)

EBB SB2209 CAN(RP2040):
https://github.com/bigtreetech/EBB
https://canbus.esoterical.online/

Umbilical Mount for CAN:
https://www.printables.com/model/326623-voron-trident-wire-cover-w-pg7-cable-gland-adapterhttps://www.printables.com/pl/model/464735-pg7-cnlinko-lp-12-mount-for-sb22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

Nozzle Clean Mod:
https://www.printables.com/model/413177-voron-trident-fixed-nozzle-scubber

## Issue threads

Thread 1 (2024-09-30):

Screen holder STL does not have indentation for audio jack port

MartijnGevaert, 2024-09-30:
Greetings, I noticed the touchscreen holder does not have a cutout for the audio jack, it does have one for the HDMI port next to it.
Simply extending the HDMI cutout to the side fixes the issue.

MartijnGevaert, 2024-09-30:
Did not see the accent part also needed.

Closed 2024-09-30.

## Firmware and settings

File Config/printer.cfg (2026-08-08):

[include mainsail.cfg]

[mcu]
canbus_uuid: YOU_DIDNT_CHANGE_ME_YET						# Insert the CANbus-UUID of your Manta from the firmware flashing steps

[mcu EBBCan]
canbus_uuid: YOU_DIDNT_CHANGE_ME_YET						# Insert the CANbus-UUID of your SB2209 RP2040 from the firmware flashing steps

[printer]
kinematics: corexy
max_velocity: 300  
max_accel: 10000
max_z_velocity: 15
max_z_accel: 350
square_corner_velocity: 5.0

[temperature_sensor MCU]
sensor_type: temperature_mcu

[temperature_sensor SoC]
sensor_type: temperature_host

#####################################################################
# 	X/Y Stepper Settings
#####################################################################

## X Stepper on Motor1(B Motor)
[stepper_x]
step_pin: PE6
dir_pin: PE5
enable_pin: !PC14
microsteps: 16
rotation_distance: 40
full_steps_per_rotation:200  #set to 400 for 0.9 degree stepper
endstop_pin: ^EBBCan:gpio24
position_min: 0
##--------------------------------------------------------------------

##	Uncomment below for 250mm build
#position_endstop: 250
#position_max: 250

##	Uncomment for 300mm build
#position_endstop: 300
#position_max: 300

##	Uncomment for 350mm build
#position_endstop: 350
#position_max: 350

##--------------------------------------------------------------------
homing_speed: 25   #Max 100
homing_retract_dist: 5
homing_positive_dir: true

##	Make sure to update below for your relevant driver (2208 or 2209)
[tmc2209 stepper_x]
uart_pin: PC13
interpolate: True
run_current: 0.9
sense_resistor: 0.110
stealthchop_threshold: 0

## Y Stepper on Motor2 (A Motor)
[stepper_y]
step_pin: PE2
dir_pin: PE1
enable_pin: !PE4
microsteps: 16
rotation_distance: 40
full_steps_per_rotation:200  #set to 400 for 0.9 degree stepper
endstop_pin: ^PF3
position_min: 0
##--------------------------------------------------------------------

##	Uncomment for 250mm build
#position_endstop: 250
#position_max: 250

##	Uncomment for 300mm build
#position_endstop: 300
#position_max: 300

##	Uncomment for 350mm build
#position_endstop: 350
#position_max: 350

##--------------------------------------------------------------------
homing_speed: 25  #Max 100
homing_retract_dist: 5
homing_positive_dir: true

##	Make sure to update below for your relevant driver (2208 or 2209)
[tmc2209 stepper_y]
uart_pin: PE3
interpolate: True
run_current: 0.9
sense_resistor: 0.110
stealthchop_threshold: 0

#####################################################################
# 	Z Stepper Settings
#####################################################################

## Z0 Stepper - Front Left on MOTOR3_A
[stepper_z]
step_pin: PB8
dir_pin: PB7
enable_pin: !PE0
# Rotation Distance for TR8x8 = 8, TR8x4 = 4, TR8x2 = 2
# rotation_distance: 4    
microsteps: 32
endstop_pin: probe:z_virtual_endstop
position_max: 250
position_min: -2.5
homing_speed: 8.0 # Leadscrews are slower than 2.4, 10 is a recommended max.
second_homing_speed: 3
homing_retract_dist: 3

##	Make sure to update below for your relevant driver (2208 or 2209)
[tmc2209 stepper_z]
uart_pin: PB9
interpolate: true
run_current: 0.6
sense_resistor: 0.110
stealthchop_threshold: 0

##	Z1 Stepper - Rear  on Motor5
[stepper_z1]
step_pin: PB4
dir_pin: PB3
enable_pin: !PB6
# Rotation Distance for TR8x8 = 8, TR8x4 = 4, TR8x2 = 2
# rotation_distance: 4  
microsteps: 32

##	Make sure to update below for your relevant driver (2208 or 2209)
[tmc2209 stepper_z1]
uart_pin: PB5
interpolate: true
run_current: 0.6
sense_resistor: 0.110
stealthchop_threshold: 0

##	Z2 Stepper - Front Right on Motor6
[stepper_z2]
step_pin: PG13
dir_pin: !PG12
enable_pin: !PG15
# Rotation Distance for TR8x8 = 8, TR8x4 = 4, TR8x2 = 2
# rotation_distance: 4  
microsteps: 32

##	Make sure to update below for your relevant driver (2208 or 2209)
[tmc2209 stepper_z2]
uart_pin: PG14
interpolate: true
run_current: 0.6
sense_resistor: 0.110
stealthchop_threshold: 0

#####################################################################
# 	Extruder
#####################################################################

#	E0 on SB2209
[extruder]
step_pin: EBBCan:gpio18
dir_pin: EBBCan:gpio19
enable_pin: !EBBCan:gpio17
microsteps: 16
rotation_distance: 22.905740611
gear_ratio: 50:10
nozzle_diameter: 0.400
filament_diameter: 1.750
heater_pin: EBBCan:gpio7
control: pid
min_temp: 0
max_extrude_only_distance: 105
max_extrude_cross_section: 2
pid_kp: 57.369
pid_ki: 2.533
pid_kd: 324.854
sensor_type: MAX31865
sensor_pin: EBBCan:gpio9
spi_software_sclk_pin: EBBCan:gpio10
spi_software_mosi_pin: EBBCan:gpio8
spi_software_miso_pin: EBBCan:gpio11
rtd_nominal_r: 100
rtd_reference_r: 430
rtd_num_of_wires: 2

[tmc2209 extruder]
uart_pin: EBBCan:gpio20
run_current: 0.65
stealthchop_threshold: 0

#####################################################################
# 	Bed Heater
#####################################################################

[heater_bed]
heater_pin: PA1
sensor_type: Generic 3950
sensor_pin: PB1
max_power: 1.0
min_temp: 0
max_temp: 115
control: pid
pid_kp: 58.437
pid_ki: 2.347
pid_kd: 363.769

#####################################################################
# 	Probe
#####################################################################

[probe]
pin: ^EBBCan:gpio22
x_offset: 0
y_offset: 0
#z_offset: 0
lift_speed: 30
activate_gcode:
    {% set PROBE_TEMP = 150 %}
    {% set MAX_TEMP = PROBE_TEMP + 5 %}
    {% set ACTUAL_TEMP = printer.extruder.temperature %}
    {% set TARGET_TEMP = printer.extruder.target %}

    {% if TARGET_TEMP > PROBE_TEMP %}
        { action_respond_info('Extruder temperature target of %.1fC is too high, lowering to %.1fC' % (TARGET_TEMP, PROBE_TEMP)) }
        M109 S{ PROBE_TEMP }
    {% else %}
        # Temperature target is already low enough, but nozzle may still be too hot.
        {% if ACTUAL_TEMP > MAX_TEMP %}
            { action_respond_info('Extruder temperature %.1fC is still too high, waiting until below %.1fC' % (ACTUAL_TEMP, MAX_TEMP)) }
            TEMPERATURE_WAIT SENSOR=extruder MAXIMUM={ MAX_TEMP }
        {% endif %}
    {% endif %}

#####################################################################
# 	Fan Control
#####################################################################
[fan]
pin: EBBCan:gpio13

[heater_fan hotend_fan]
pin: EBBCan:gpio14
heater: extruder
heater_temp: 70.0


[fan_generic nevermore]
##	Print Cooling Fan - CNC_FAN0
pin: PF8
kick_start_time: 0.5
off_below: 0.10

[controller_fan controller_fan_1]
##	Hotend Fan - CNC_FAN1
pin: PF9
max_power: 1.0
kick_start_time: 0.5
fan_speed: 0.66


[heater_fan controller_fan_2]
##	Controller fan - CNC_FAN2
pin: PF6
kick_start_time: 0.5
heater: heater_bed
heater_temp: 80
fan_speed: 0.66

[fan_generic exhaust_fan]
#	Exhaust fan - CNC_FAN0
pin: PF7
max_power: 1.0
shutdown_speed: 0.0
kick_start_time: 0.5

#####################################################################
# 	LED Control
#####################################################################

[neopixel toolhead_light]
pin: EBBCan:gpio16
chain_count: 3
color_order: GRBW

[output_pin caselight]
#Chamber Lighting - HE3 Connector
pin: PA3
pwm:true
shutdown_value: 0
cycle_time: 0.01

#####################################################################
# 	Homing and Gantry Adjustment Routines
#####################################################################

[idle_timeout]
timeout: 3300

[safe_z_home]
##--------------------------------------------------------------------

##	Uncomment below for 250mm build
#home_xy_position: 125,125

##	Uncomment below for 300mm build
#home_xy_position: 150,150

##	Uncomment below for 350mm build
#home_xy_position: 175,175

##--------------------------------------------------------------------
speed: 100
z_hop: 10

[z_tilt]

##--------------------------------------------------------------------
## Uncomment below for 250mm build
#z_positions:
#    -50, 18
#    125, 298
#    300, 18
#points:
#    30, 5
#    125, 195
#    220, 5

## Uncomment below for 300mm build
#z_positions:
#   -50, 18
#   150, 348
#   350, 18
#points:
#   30, 5
#   150, 245
#   270, 5

## Uncomment below for 350mm build
#z_positions:
#   -50, 18
#   175, 398
#   400, 18
#points:
#   30, 5
#   175, 295
#   320, 5

##--------------------------------------------------------------------

speed: 200
horizontal_move_z: 10
retries: 5
retry_tolerance: 0.0075


[bed_mesh]
mesh_min: 10,10
##--------------------------------------------------------------------

##	Uncomment below for 250mm build
#mesh_max: 240,240

##	Uncomment below for 300mm build
mesh_max: 290,290


##	Uncomment below for 350mm build
#mesh_max: 340,340

##--------------------------------------------------------------------



########################################
# EXP1 / EXP2 (display) pins
########################################
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

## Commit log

2024-05-31 add stl and cleanup
    [Anchor v2.stl, HDMI5 Screen Holder.stl, M8P_Mounting bracket.STL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]
2024-07-12 Rename HDMI5 Screen Holder.stl to HDMI5 V1.1 Screen Holder.stl
    [HDMI5 Screen Holder.stl, HDMI5 V1.1 Screen Holder.stl]
2025-12-15 pin fix
    [printer.cfg]
2025-12-21 mainsail fix
    [printer.cfg]
2026-06-13 Fix #10
    Fixes #10
    [printer.cfg]
